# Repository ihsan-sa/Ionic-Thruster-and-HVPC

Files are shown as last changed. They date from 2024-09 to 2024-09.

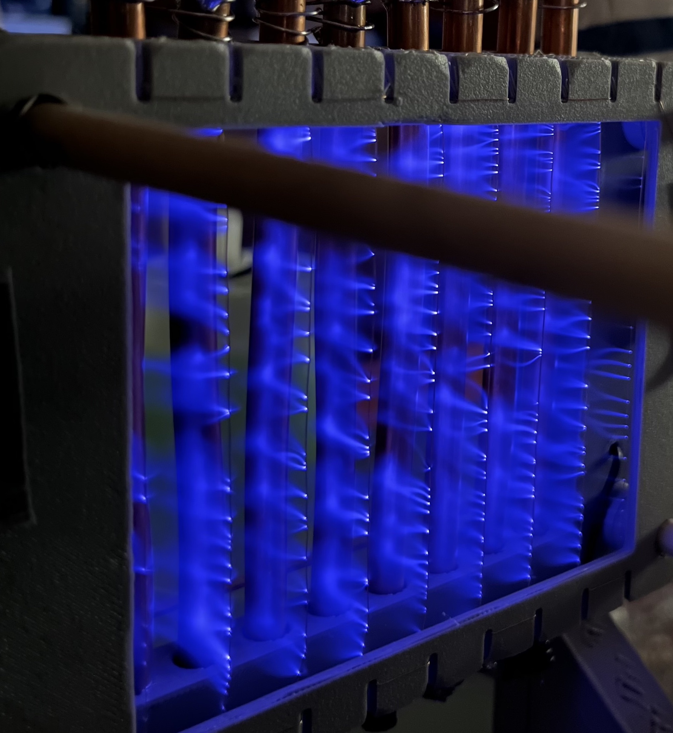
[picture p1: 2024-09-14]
IonicThruster/EHD-Image1.jpg

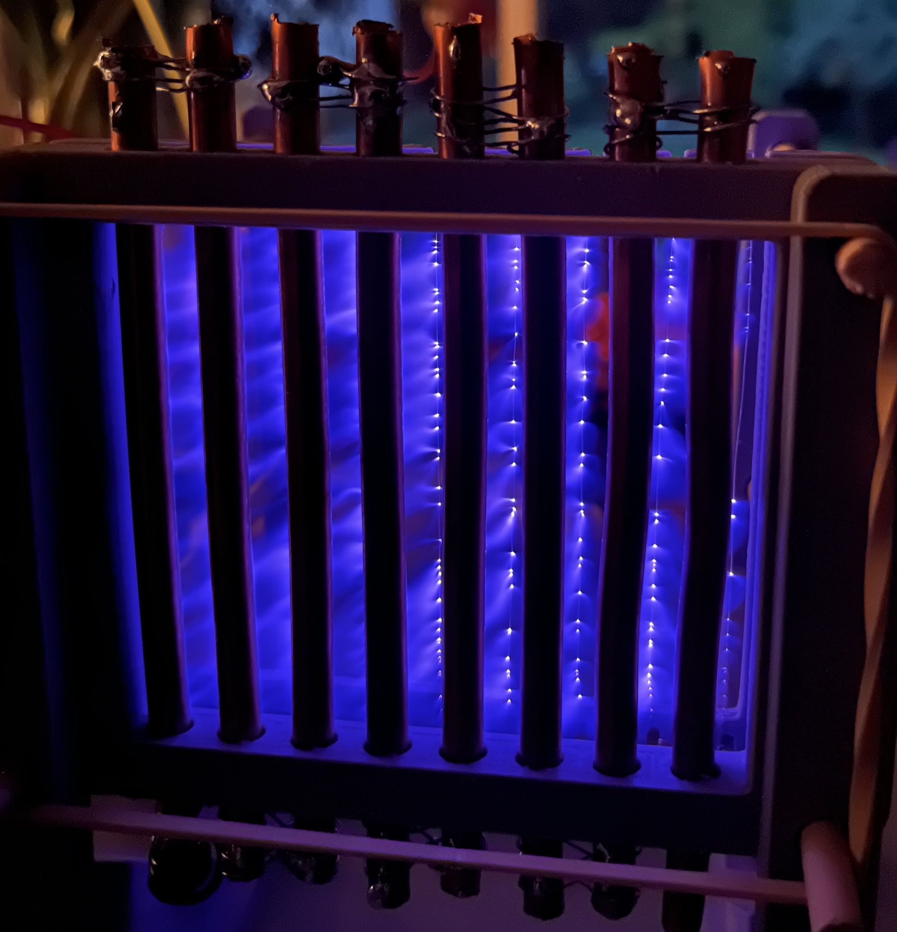
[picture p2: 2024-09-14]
IonicThruster/EHD-Image2.jpg

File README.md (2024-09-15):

# Electrohydrodynamic (EHD)/Ionic Thruster and 50kV 100W High Voltage Power Converter (HVPC)

The aim of this project was to construct a working EHD thruster powered by a custom 50kV 100W Flyback HVPC.
You may find my LinkedIn post about my project here: [https://www.linkedin.com/in/ihsan-salari-6957aa221/](https://www.linkedin.com/posts/ihsan-salari-6957aa221_iam-excited-to-share-the-subject-of-my-research-activity-7090835072915816448-yWUP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)

This project was split into four parts:
1. Building the HVPC
2. Building the EHD thruster
3. Conducting the research experiment, which answered the research question: 
To what extent does the spacing of electrode pairs affect the thrust produced by a single-stage electrohydrodynamic
(EHD) thruster with two electrode pairs in parallel operation?
4. Answering the research question by deriving the theoretical results of the experiment from MIT's ionic thruster research and my own original approach.

All four parts of this project were successfully completed. More information about each step can be found in the following places:
1. For more information about the research, and the general functioning of an EHD  thruster, please see the EHD thruster research overview document in the main folder.
2. For schematics, 3D files and images, please see the respective ionic-thruster and HVPC folders.
3. For the research paper abstract, please see the PDF in the main folder.

EHD1

IonThrusterMesuringDevice v5 Image

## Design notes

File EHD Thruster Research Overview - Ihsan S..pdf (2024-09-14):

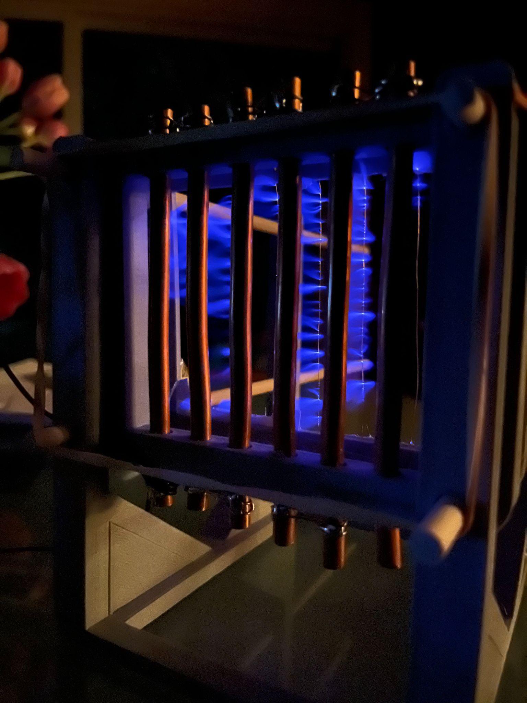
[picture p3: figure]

Electrohydrodynamic (Ionic) Thruster Design
Below is a brief overview of the current EHD thruster and high voltage power converter design. The system is currently operational and lab testing is underway.

An EHD thruster is a device which creates a flow of air (ionic wind) through the electrostatic forces between bodies of different curvature and voltage potential (eg. A thin wire and large tube). Figure 1 to the left shows the EHD thruster in operation. This video (https://youtu.be/MWuXdMzDU_8) shows my thruster in operation as well. The purple glow is the plasma created via corona discharge. This video (https://youtu.be/K1aXm_3OO9c?si=4j44ZHx2rCBi9skS) I made explains the thruster working principle.
Figure 1 (left): One of my EHD thrusters in operation.

Research Focus
The focus of this research is to determine the relationship between the distance between electrode pairs and the thrust produced by the thruster. A large spatial presence is a weakness of this technology, and thus, optimizing the thrust per unit volume is key. Here, we explore this issue with regards to electrode pair interaction. Graph 1 shows the preliminary results for this relationship, suggesting an optimal electrode pair spacing of between 2 to 4 cm.

Thruster Construction:
A 3D printed structure (Figure 3), holds up the cathode and anode. The cathode (emitter) is a high gauge wire of 34.5 AWG and the anode (collector) is a 6.35mm copper tube, preventing unwanted corona discharges (due to its corona inception voltage of around 70kV). The EHD thruster takes 50kV DC as its input, provided by a custom built high voltage power converter.

High Voltage Power Converter (HVPC):
Safe Operation Guidelines Document (https://docs.google.com/document/u/0/d/1ApY4CR1cqmoRC1JgjLDbcgATw5IxUNA8D5NUii_cCfc/edit)

The fully custom built HVPC, which steps up 30VDC to 50kVDC. 30VDC from a 5A power pack powers a 555 timer circuit which outputs a 13kHz square wave with 50% duty cycle. This is fed to a power MOSFET, which pulses power to the primary of a custom made alternating current flyback transformer. The output of the flyback is around 3-4kV ac. The flyback supplies a 4 stage half bridge

Cockcroft-Walton voltage multiplier, which steps the voltage up to 50kV. The voltage multiplier, and later the transformer, is kept in oil in order to prevent arcing. The IRFP260N MOSFET is attached to a 2x3cm finned heat sink in order to dissipate heat and improve efficiency. Please refer to Figures 2, 4 and 5 below for more information about HVPC design.

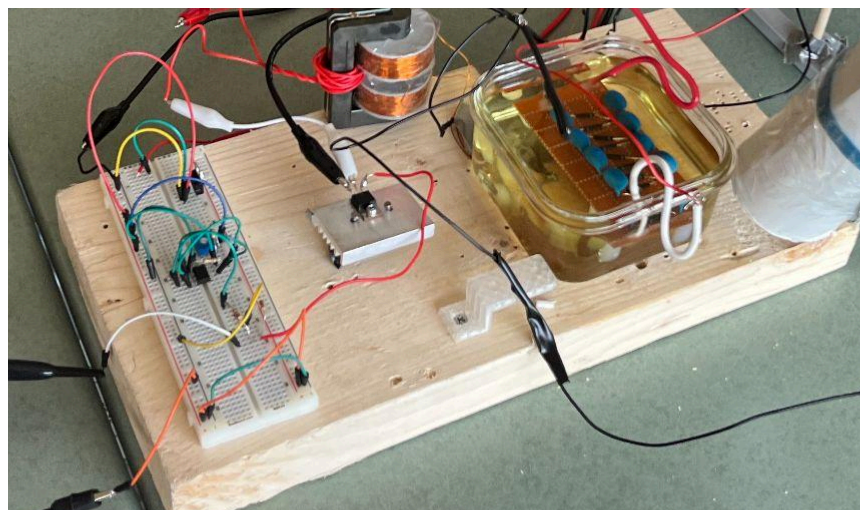
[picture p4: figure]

Figure 2: Image of the HVPC V1. V2 uses a larger power MOSFET (IRFP260N) and a transformer submerged in oil.

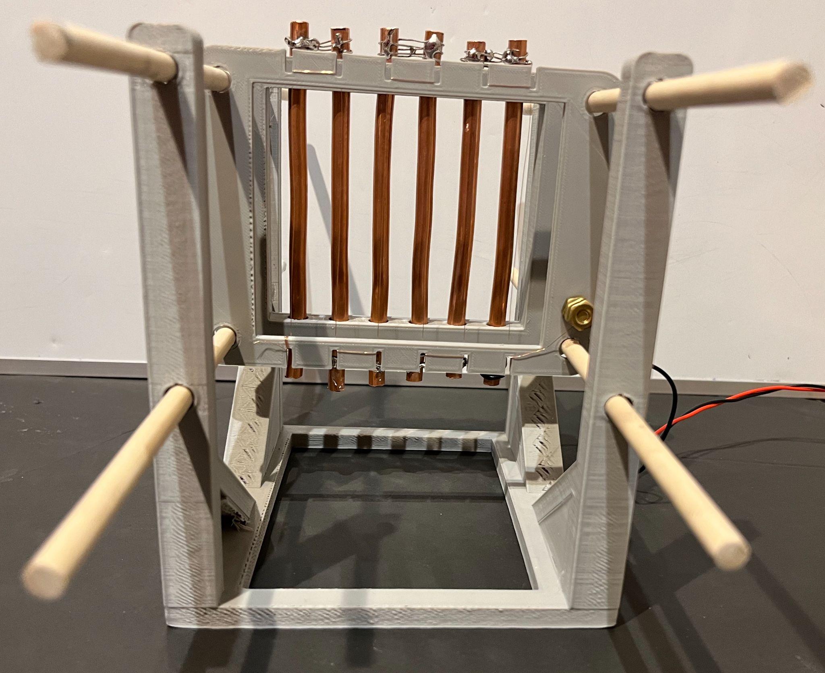
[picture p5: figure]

Figure 3 - Image of EHD thruster Design

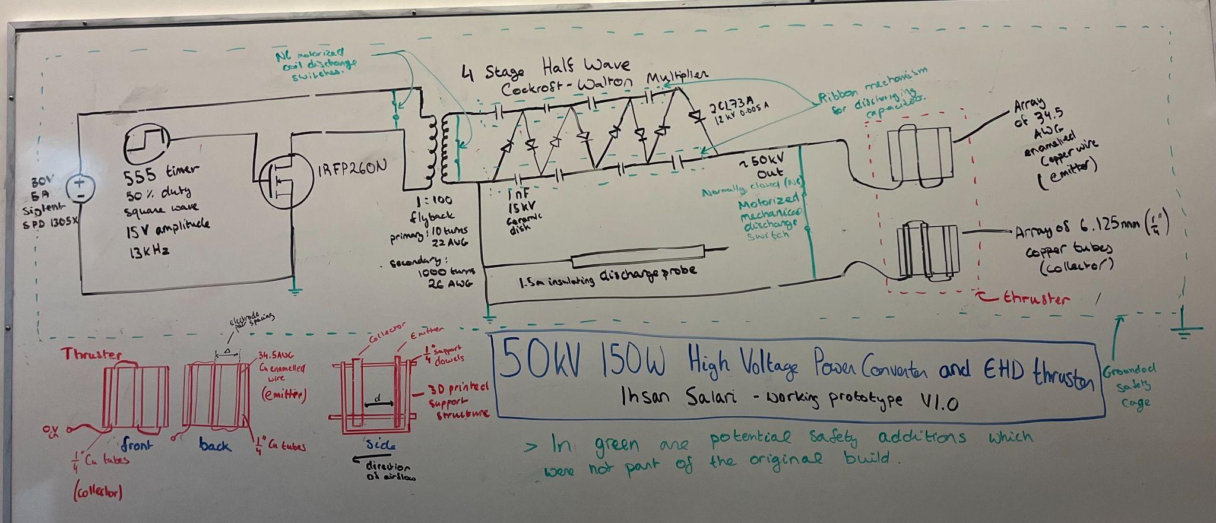
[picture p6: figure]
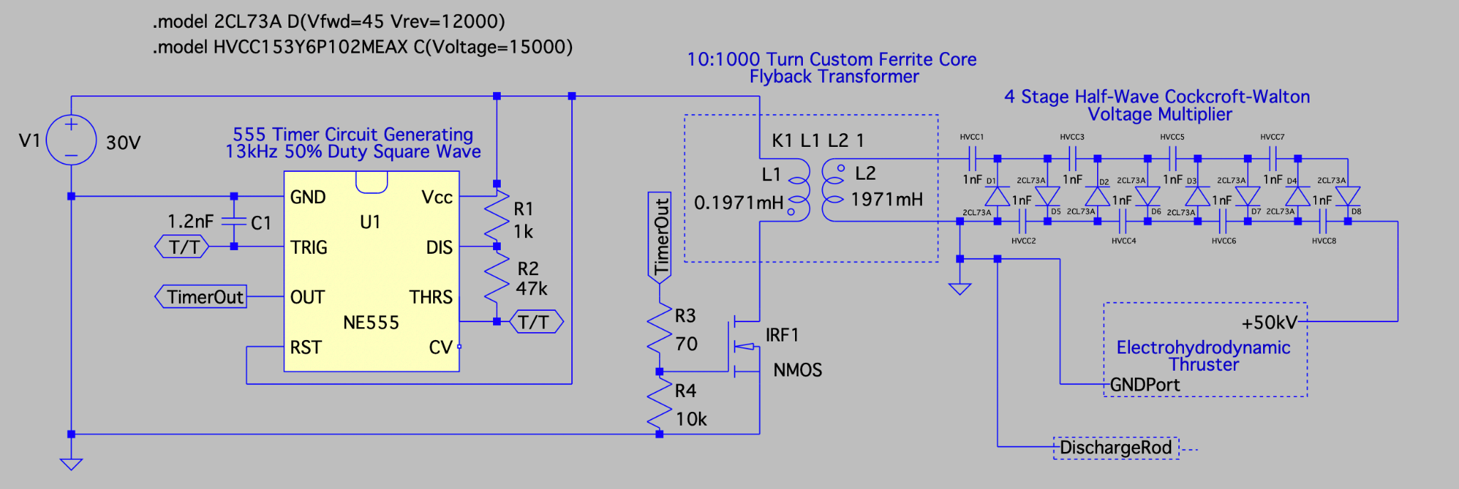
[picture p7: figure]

Figure 4 (top) and 5 (below): System Schematics. The green writing outlines potential safety modifications to the original design.

Building Process

The first step was understanding common high voltage power converter topologies and drivers, which I extensively researched. I looked into three main areas: transformers, resonant inverters and oscillator driver circuits, and voltage multipliers. I then ran many simulations in LTSpice before testing prototypes. My first version of the high voltage power converter (HVPC) consisted of a mains transformer which I wound to step up the voltage to a few kV. However, this design did not work, popping the breaker due to too low of an impedance and wrong transformer core material choice. I then pivoted and built a DC flyback converter based topology, which successfully generated a few kV. Finally, I wound my own AC flyback transformer and built a 4 stage half bridge Cockcroft-Walton voltage multiplier. The thruster construction was quite straightforward and I built many iterations of the electrode spacing layout to obtain the highest wind speed possible. I then built the final test structure which I used to vary the electrode pair spacing and experimentally determine the optimal spacing, as showcased in my research. Switching out the small MOSFET with a larger IRFP260N power MOSFET submerged in water for better cooling drastically increased the max power of the thruster. The most thrust I generated was with a large electrode pair spacing of 10cm and totaled 4g of thrust, or about 39mN. Upon reaching out to Caltech, University of Waterloo and University of British Columbia professors in the field, I received very supportive
comments, despite the fact that no direct technical advice could be given due to liability concerns.

Preliminary Results and Experimental Setup

Graph 1: Distance Between Electrode Pairs (cm/±0.1) vs Thrust Produced (mN)

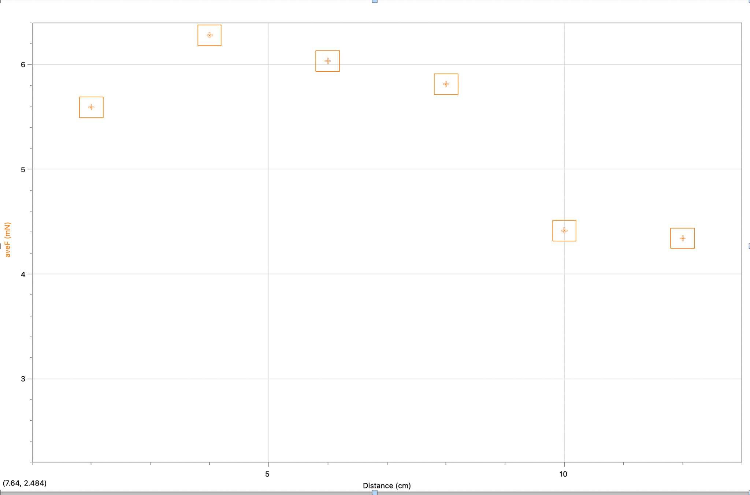
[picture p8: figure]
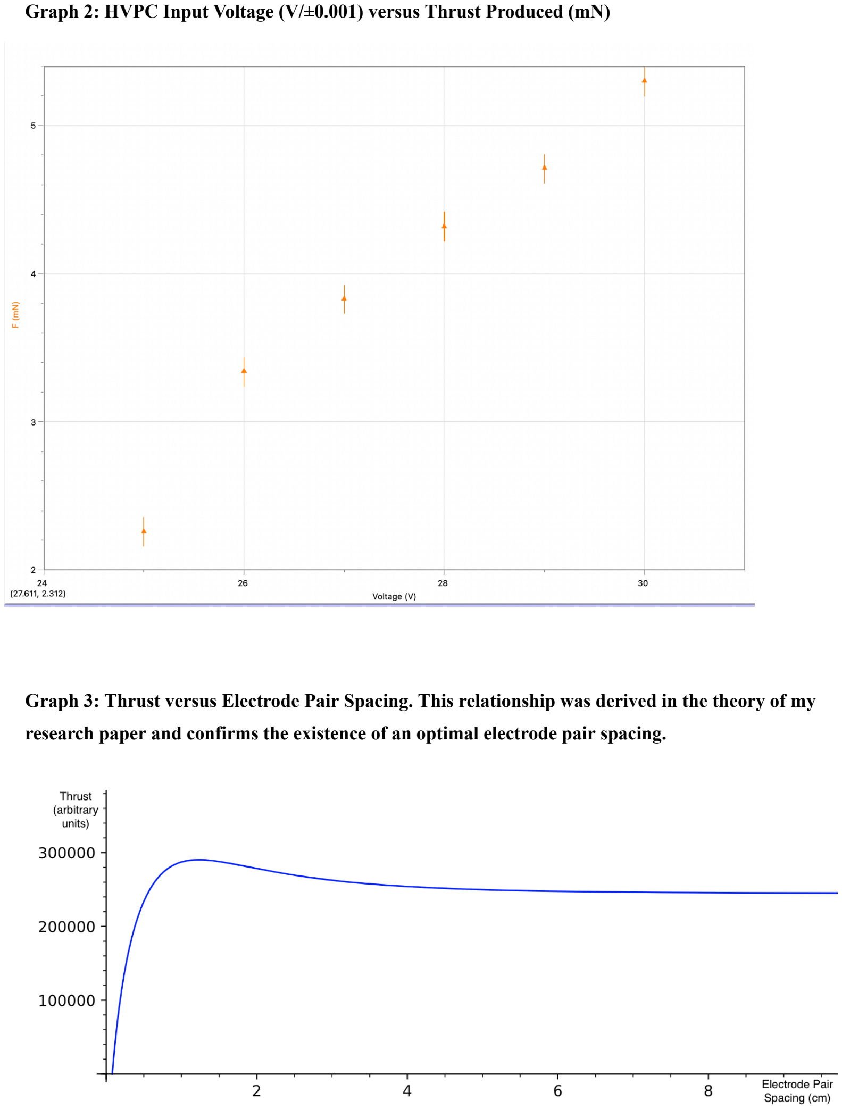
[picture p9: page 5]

Graph 2: HVPC Input Voltage (V/±0.001) versus Thrust Produced (mN)

Graph 3: Thrust versus Electrode Pair Spacing. This relationship was derived in the theory of my research paper and confirms the existence of an optimal electrode pair spacing.

Research Paper Abstract - Available in Research Supplement

Previous work has shown electrohydrodynamic (EHD) propulsion methods to be a potential alternative to conventional means of aircraft propulsion. This technology emits no greenhouse gasses, is quieter than conventional propulsion methods, and has been shown to have a similar thrust to power ratio. However, spatial demands limit the widespread adoption of EHD thrusters. In this paper, we address spatial optimization of single stage EHD thrusters consisting of two wire-to-cylinder electrode pairs. We confirm the existence of an optimal electrode pair spacing for this thruster geometry. Previous efforts by Gilmore

and Barrett (MIT) have estimated a maximum thrust per unit area of 3. 3Nm . We extend their work by

−1

deriving and calculating the optimal electrode pair spacing with respect to the inter-electrode distance d. The findings presented in this paper will enable the construction of more spatially efficient EHD thrusters, allowing this technology to become a viable option for an increased number of applications.

References

[1] https://www.nature.com/articles/s41586-018-0707-9 (Flight of an Aeroplane with Solid State Propulsion)
[2] http://dx.doi.org/10.1109/compel.2017.8013315 ( Design and implementation of a lightweight high-voltage power converter for electro-aerodynamic propulsion
[3] https://royalsocietypublishing.org/doi/epdf/10.1098/rspa.2014.0912 (Electrohydrodynamic thrust density using positive corona-induced ionic winds for in-atmosphere propulsion)
[4] https://royalsocietypublishing.org/doi/epdf/10.1098/rspa.2012.0623 (On the performance of electrohydrodynamic propulsion)

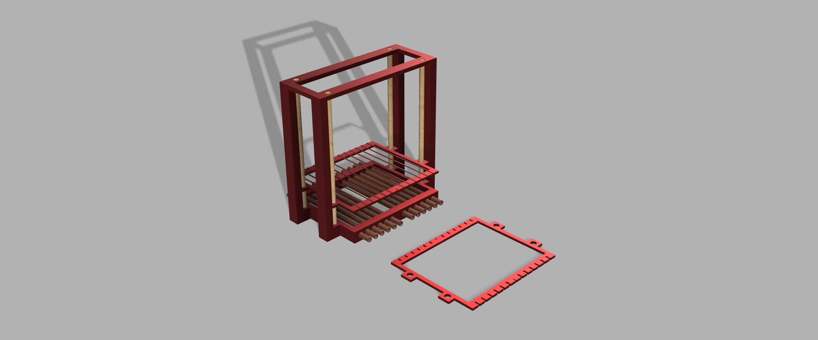
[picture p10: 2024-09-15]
IonicThruster/IonThrusterMesuringDevice v5 Image.png

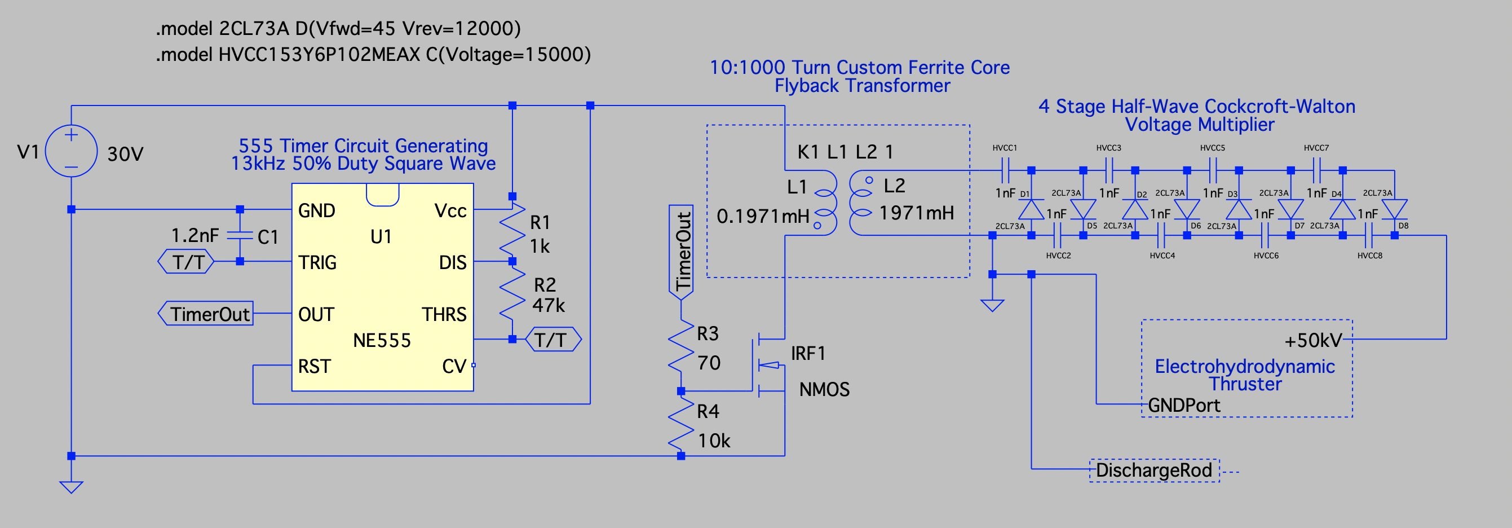
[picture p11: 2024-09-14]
HVPC/Circuit-Diagram.png

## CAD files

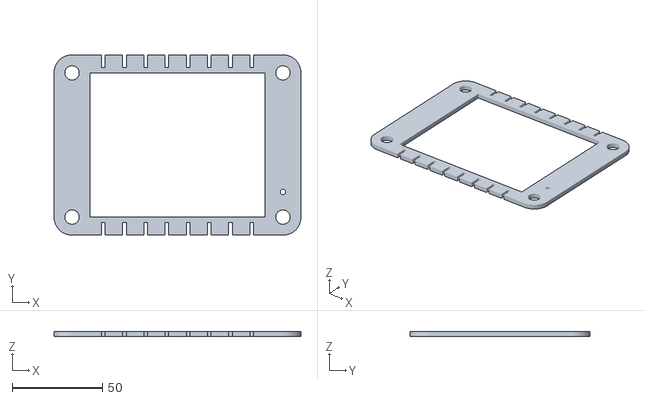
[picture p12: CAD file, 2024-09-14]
IonicThruster/3D-Designs/Emitter.stl
137.0 x 100.0 x 3.00

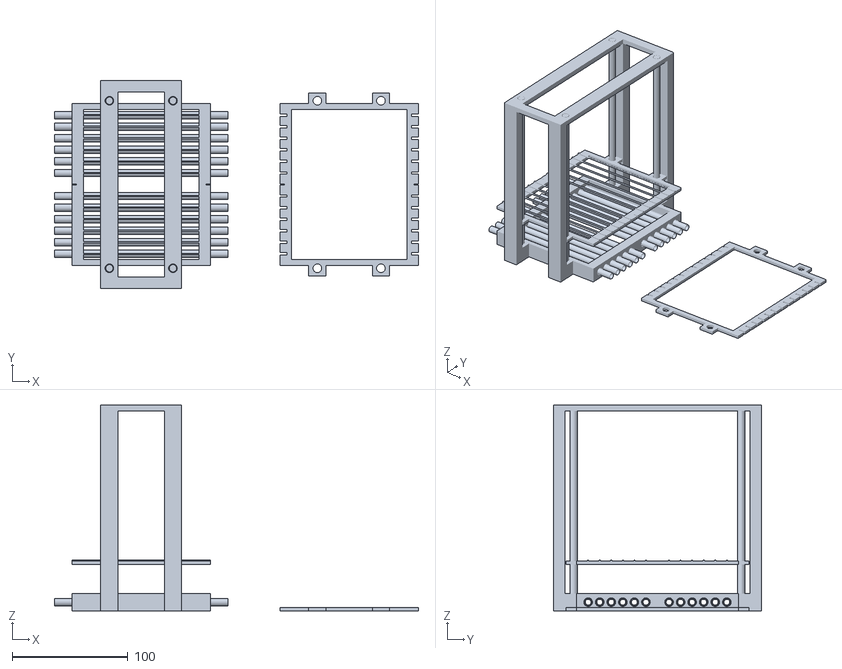
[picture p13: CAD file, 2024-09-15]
IonicThruster/IonThrusterMesuringDevice v5.stl
315.0 x 180.0 x 178.0

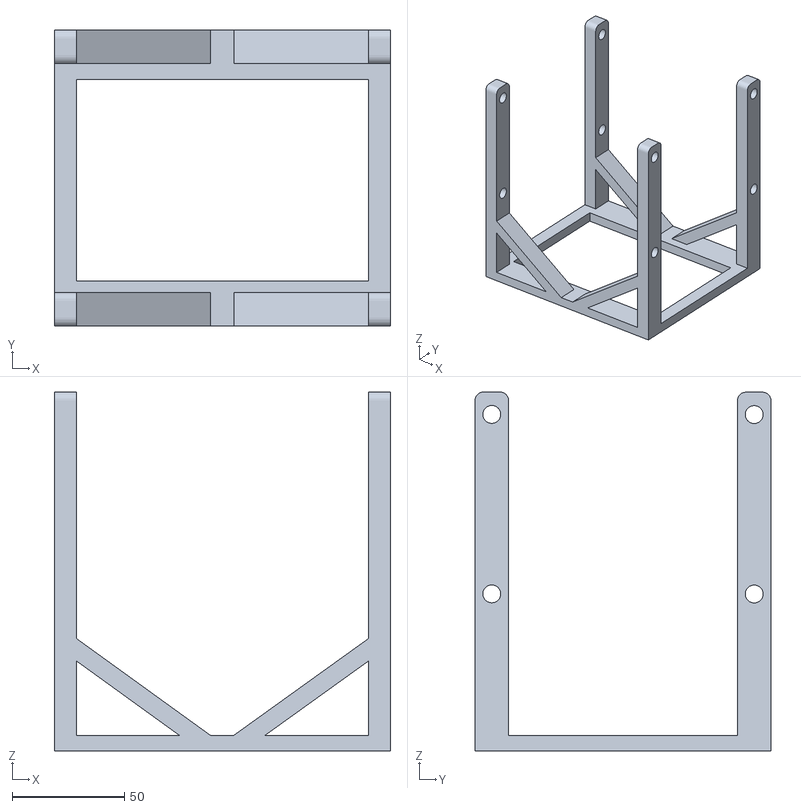
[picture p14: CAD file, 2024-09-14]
IonicThruster/3D-Designs/Stand.stl
150.0 x 132.0 x 160.1

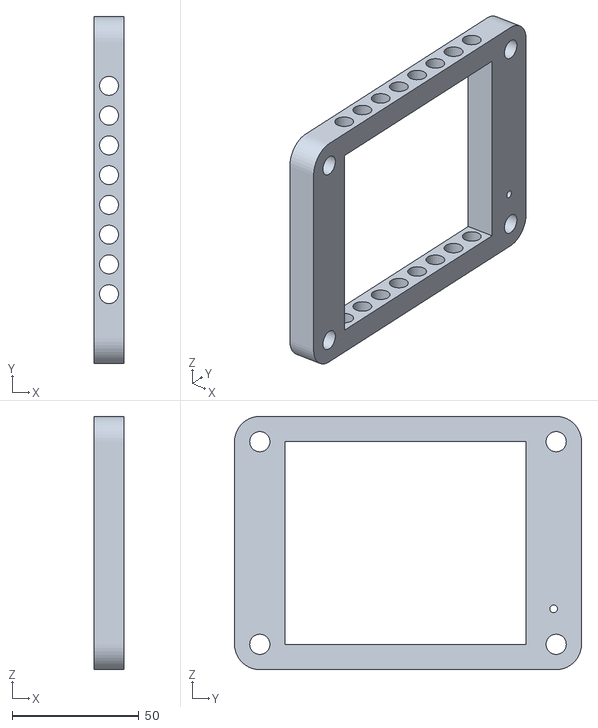
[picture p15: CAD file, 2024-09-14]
IonicThruster/3D-Designs/Collector.stl
12.0 x 137.0 x 100.0
